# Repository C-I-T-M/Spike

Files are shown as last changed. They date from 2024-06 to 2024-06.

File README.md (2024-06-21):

# Spike
Dentro de este GIT encontrarán todo lo necesario para utilizar y/o armar a spike.

RECOMENDACION: Leer primero el manual técnico y de usuario y después el manual de armado e iniciación. En este último realizar los procesos de forma secuencial (no armar y luego calibrar)

Si consideran que falta información o tienen alguna duda favor de contactarme.
Contacto: citm0220@gmail.com

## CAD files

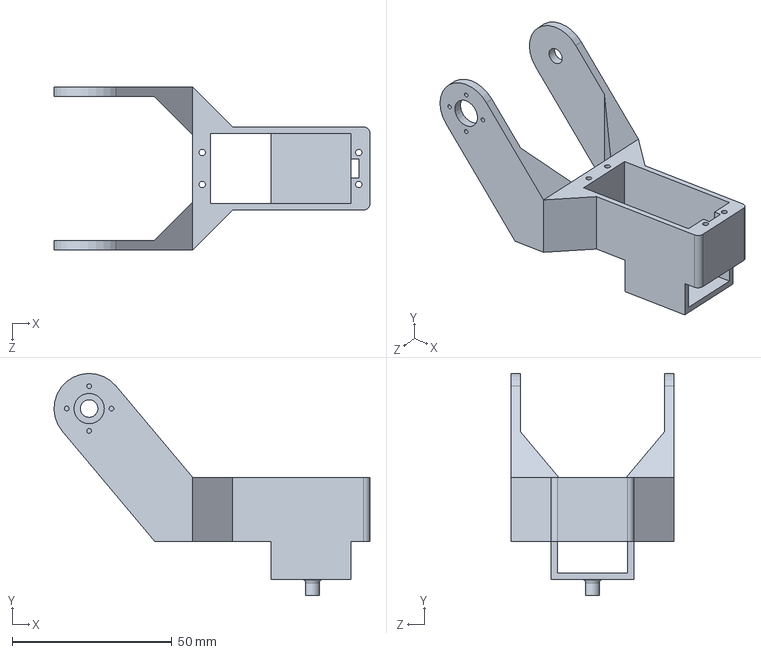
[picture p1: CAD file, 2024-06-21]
Piezas/femur_izquierdo.SLDPRT
98.9 x 69.5 x 51.0 mm

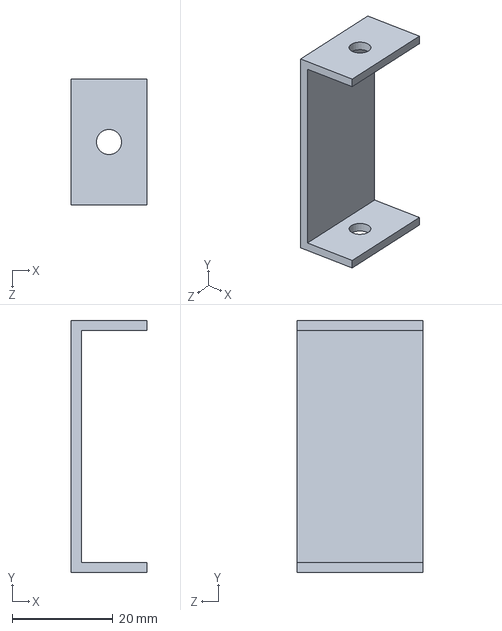
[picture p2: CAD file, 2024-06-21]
Piezas/SoporteLargo.SLDPRT
15.0 x 50.0 x 25.0 mm

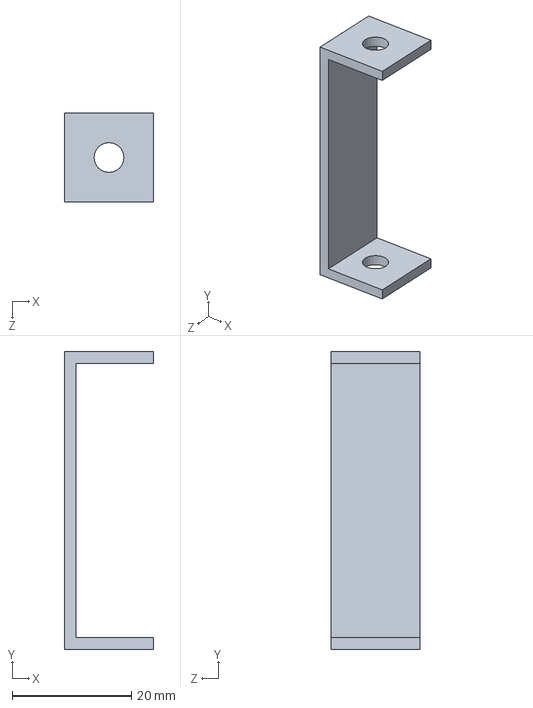
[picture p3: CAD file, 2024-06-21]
Piezas/SoporteCorto.SLDPRT
15.0 x 50.0 x 15.0 mm

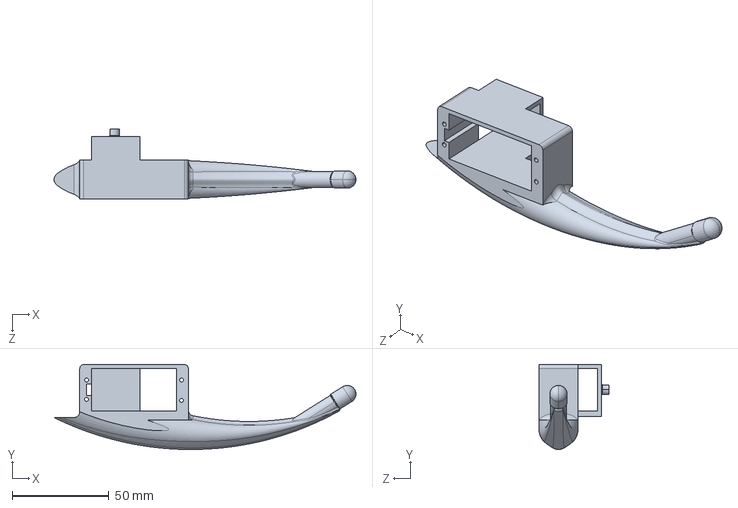
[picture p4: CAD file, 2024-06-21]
Piezas/tarso_izquierdo.SLDPRT
155.8 x 43.8 x 36.3 mm

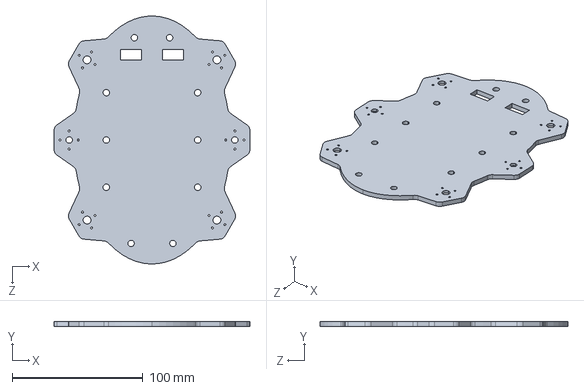
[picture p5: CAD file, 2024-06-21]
Piezas/Base.SLDPRT
150.0 x 3.50 x 190.0 mm

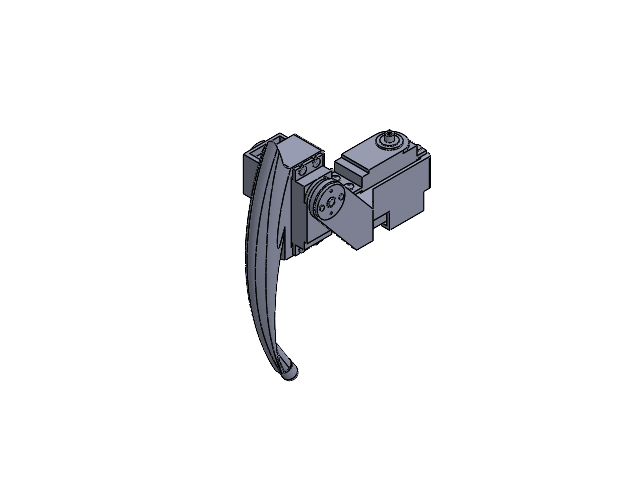
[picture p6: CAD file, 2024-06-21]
Piezas/pata_izquierda.SLDASM
femur_izquierdo
pataai.STEP
conector_cirular
Servomotor x 2
tornillo A
tornillo B x 8
tornillo C x 2

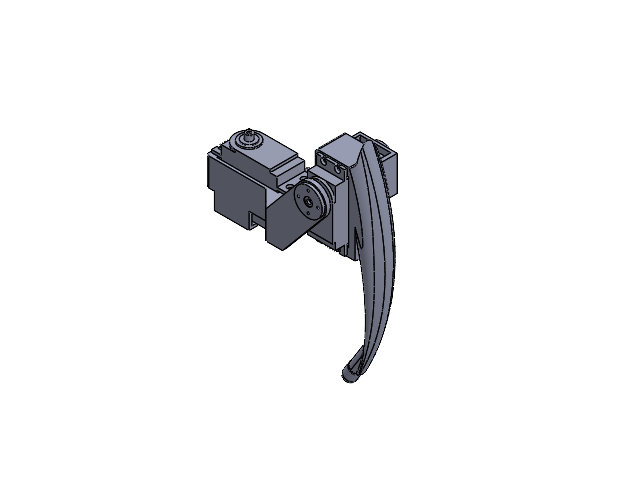
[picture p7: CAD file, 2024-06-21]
Piezas/pata_derecha.SLDASM
conector_cirular
Servomotor x 2
femur_derecho
pataad.step

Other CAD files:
Piezas/femur_derecho.SLDPRT
Piezas/tarso_derecho.SLDPRT

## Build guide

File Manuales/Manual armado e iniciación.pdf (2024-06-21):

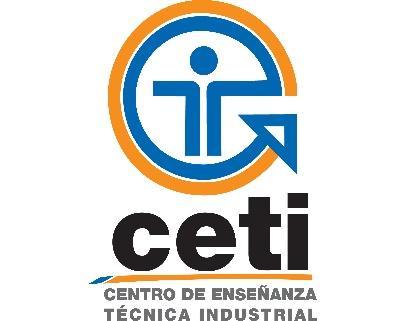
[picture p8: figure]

Spike

CENTRO DE ENSEÑANZA TÉCNICA INDUSTRIAL

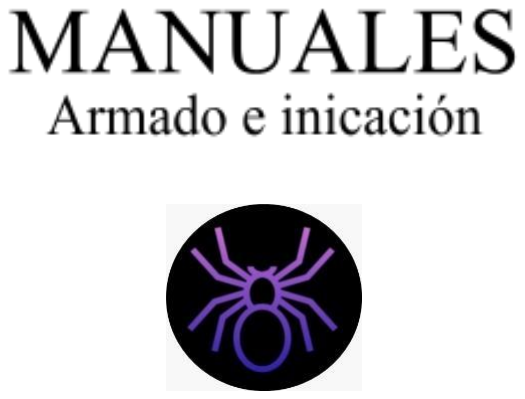
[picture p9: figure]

Alumnos:

Arien Michelle López Jáuregui 20300712

Carlos Isaac Torres Méndez 20300715

Esteban Barboza Ochoa 20300719

Carrera:

Control automático e Instrumentación

Asesor:

Ph.D Alfonso Pérez Gonzales

Asesor externo:
Ing. Carlos Barboza Ochoa
Ph.D. César Méndez García

ÍNDICE

MANUAL ARMADO E INICIACIÓN

INTRODUCCIÓN

En este documento se mostrará y detalla todo lo necesario para el funcionamiento de Spike.

OBJETIVO
Explicar cómo hacer el armado de Spike, cómo hacer la iniciación del robot y las calibraciones que lleguen a ser necesarias para su buen funcionamiento.

LISTA DE PARTES:
Pieza | Cantidad | Imagen

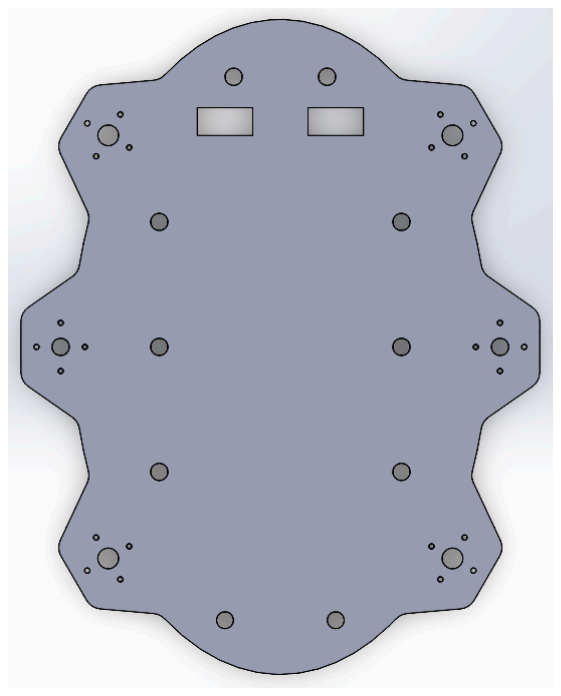
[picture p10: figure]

Base (Imprimir) | 2

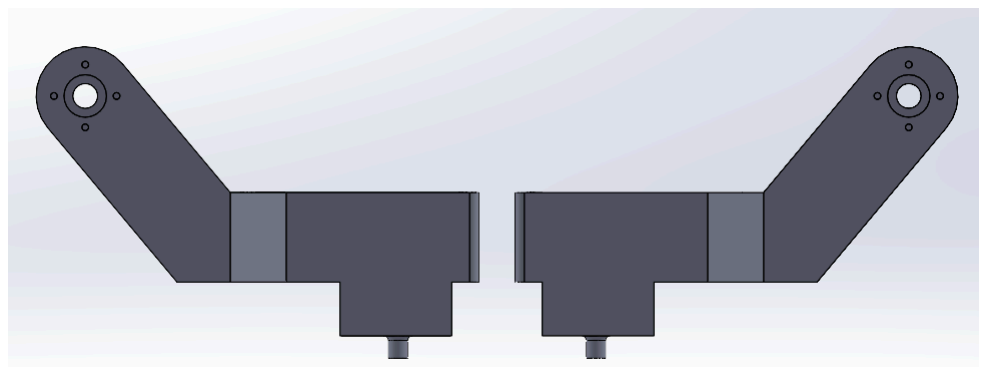
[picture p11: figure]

Fémur (Imprimir) | 3 derecho 3 izquierdo

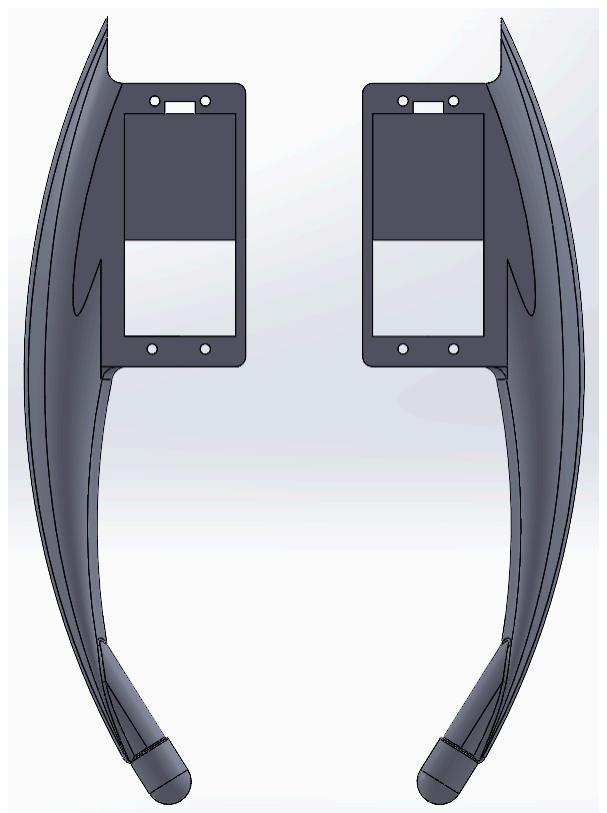
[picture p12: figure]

Tarso (Imprimir) | 3 derecho 3 izquierdo

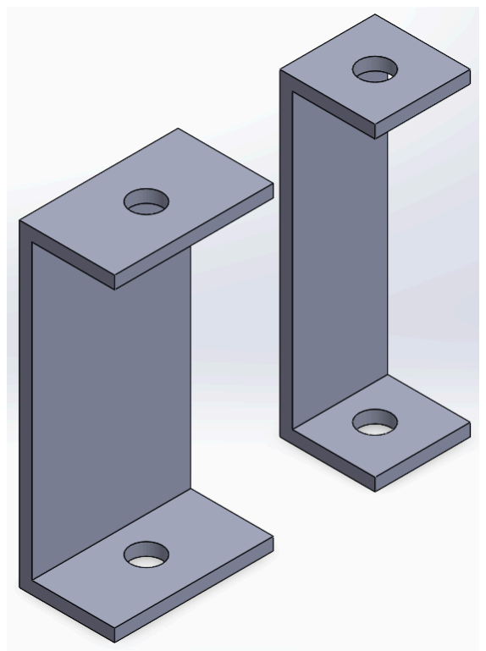
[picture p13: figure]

Soportes | 4 largo 4 corto

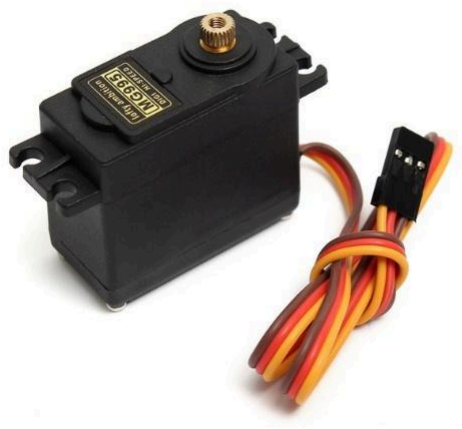
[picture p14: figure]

Servomotor MG995 (compra externa) | 12
Módulo Controlador de servos PCA9685 | 1

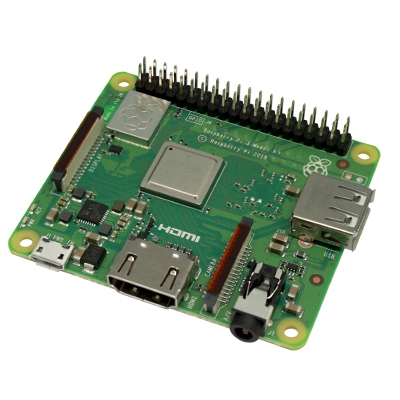
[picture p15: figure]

Raspberry:
Recomendamos
modelos con
bluetooth integrado
(como la PI 3
modelo A+ o la
Zero o Zero 2W) si
se quiere utilizar la
app, en caso de no
querer usar esta
función, se pueden
usar otros modelos.

1

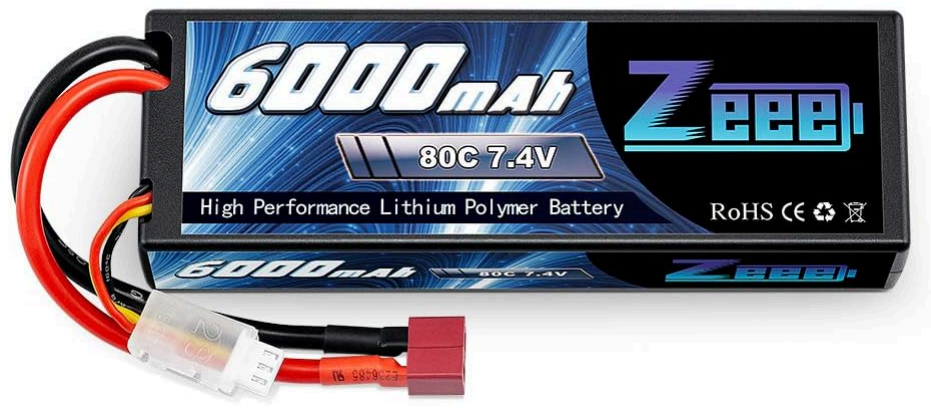
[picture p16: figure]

Batería LiPo | 1

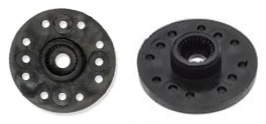
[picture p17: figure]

Conector circular (Incluida en servos) | 12
Tornillo A (Incluido en servos) | 12
Tornillo B (Incluido en servos) | 24

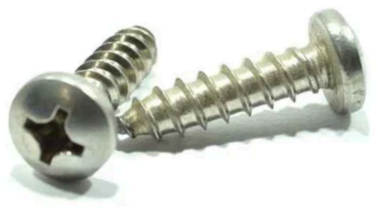
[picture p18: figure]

Tornillo C #2 x 3/8" (compra externa) | 12

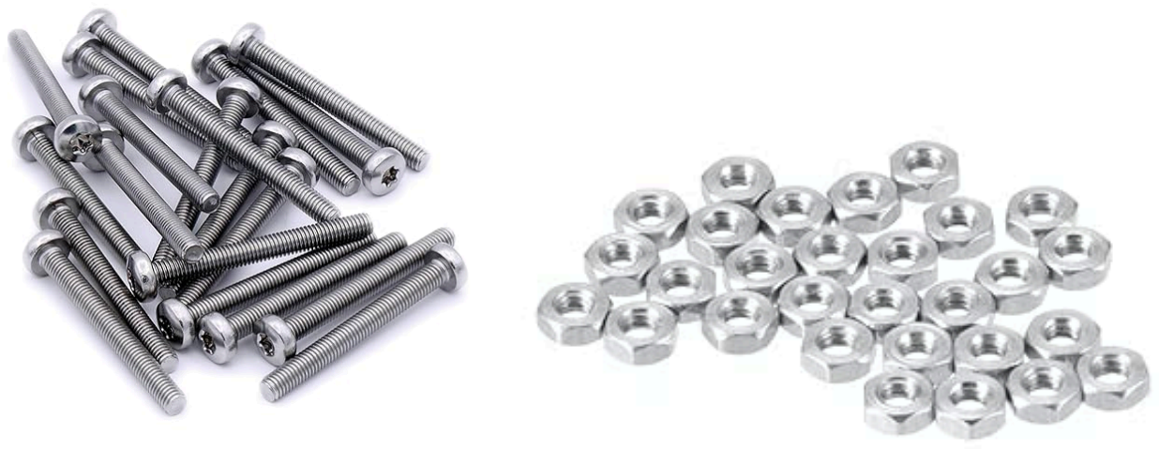
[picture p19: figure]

Tornillo D M1.6 x 10 mm + tuercas (compra externa) | 12
Tornillo E 1/8“ x 1/2 + tuercas (compra externa) | 14

CALIBRACIÓN DE SERVOS:

IMPORTANTE: solo realizar este apartado en caso de usar un modelo de servomotor diferente al MG995.

Para el lograr una calibración de servos seguir los siguientes pasos:

- Investigar la datasheet del servomotor a utilizar y buscar los siguientes datos:
- Frecuencia de funcionamiento.
- pulse width para 0 grados
- pulse width para 180 grados
- Poner el conector circular al servo para que sea más sencillo visualizar los ángulos de los giros.
- Conectar un servo al módulo PCA9685, el cual fue conectado previamente a la raspberry como se muestra en el diagrama de conexión (manual técnico).
- Abrir el código “Motores.py” y realizar lo siguiente:
- En caso de encontrar los valores en la datasheet:
■ Dentro de la variable puls_0 guardar el valor del pulse width para 0 grados. ■ Dentro de la variable puls_180 guardar el valor del pulse width para 180 grados.
■ Dentro de la función pwm.set_pwm_freq() ingresar el valor de la frecuencia de funcionamiento.
■ Iniciar el código y verificar que en efecto el servo gire de 0 a 180 grados, en caso contrario, realizar ajustes a prueba y error de los valores de puls_0 y puls_180.

- En caso de no encontrar los valores en la datasheet, utilizar los puestos en el código como referencia y realizar los ajustes necesarios.

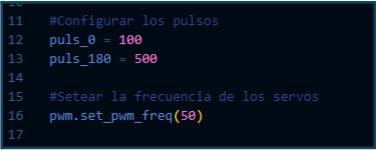
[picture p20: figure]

- El código realizará la siguiente secuencia (se puede modificar la variable de tiempo entre movimientos t si el usuario lo ve necesario):
- Girar 0 grados y esperar
- Girar 90 grados y esperar
- Girar 180 grados y esperar

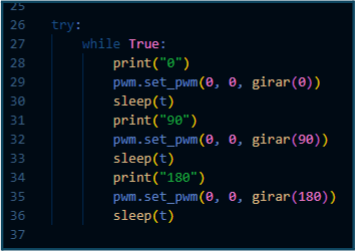
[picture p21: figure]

- La importancia de probar con estos 3 ángulos radica en que podría pasar que los servos giran 0 y 180 grados, pero no tengan el pulse width correcto (sucede cuando se eligen valores menores al correcto de 0 y mayores al correcto de 180), entonces el resto de ángulos no serán correctos. Para ello agregamos el ángulo de 90º.

- Si los tres ángulos son correctos, el servo estará calibrado, en caso contrario realizar las modificaciones necesarias.
- Verificar que funcione correctamente para todos los servomotores que se quieran utilizar.

ARMADO:
Para el apartado de armado del robot seguir los siguientes pasos:
- Conectar los servos al módulo de relevadores previamente conectado a la raspberry. La conexión de servos a módulo puede ser arbitraria.

IMPORTANTE: no tener armada ninguna parte del robot, los servos deben estar sueltos.

- Utilizando el código “Principal.py”, descomentar el bloque “while True”. Dentro de él, descomentar tarsos90() y femurs90(). Deja comentado el resto y corre el código; esto hará que todos los servos tengan un ángulo de 90 grados para poder ser unidos al resto de partes.

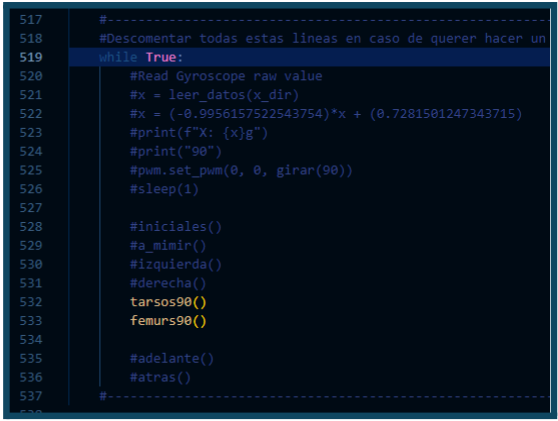
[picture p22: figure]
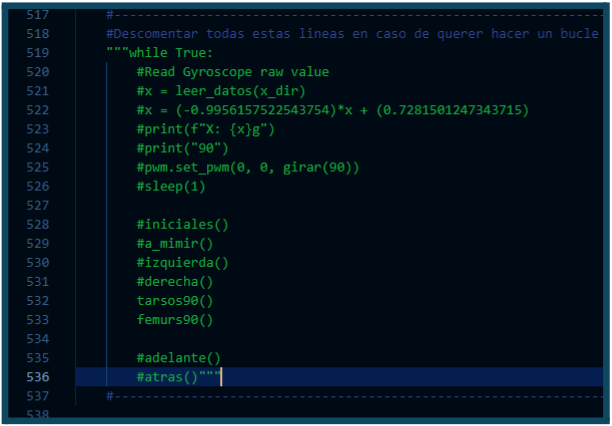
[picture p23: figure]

- Desconectar los servos del módulo y colocarlos en tarso y fémur, asegurándolos con los tornillos B. Unir el conector circular al fémur usando dos tornillos C y agregar la pieza del tarso con su motor usando la pieza circular como conexión, y un tornillo A para asegurar que quede sujeto.

Asegurarse que el motor tenga un ángulo de 90° en relación al fémur, como se muestra en las imágenes de referencia.

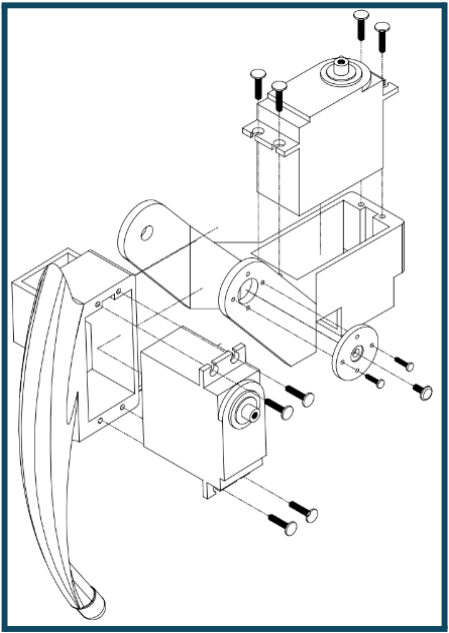
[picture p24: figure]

Repetir este paso con las 6 patas.

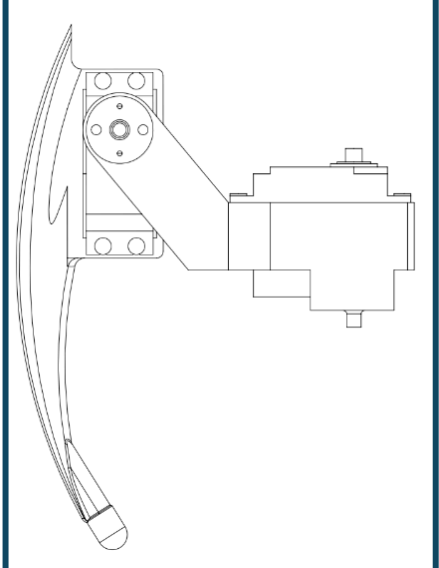
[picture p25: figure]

- Tomar una base, poner los conectores circulares donde se encuentran las hendiduras y asegurarlos bien utilizando los Tornillos D con sus respectivas tuercas.

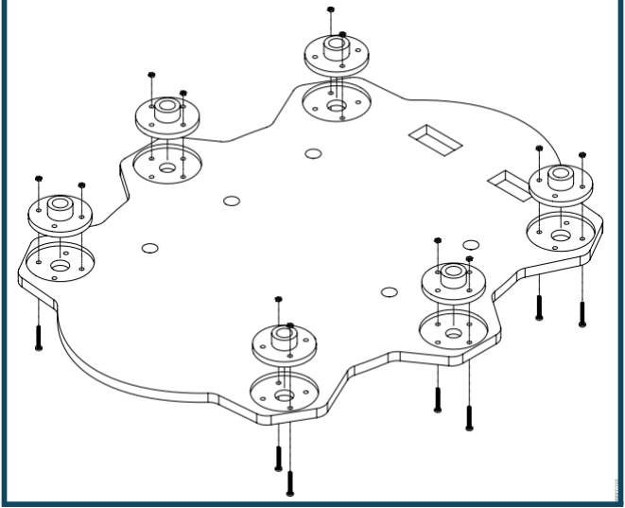
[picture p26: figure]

- Lo siguiente es agregar las piezas de las patas con ayuda de los tornillos A y los conectores circulares.

IMPORTANTE: las patas deben tener un acomodo como se muestra en la imagen.

TIP: conectar los servos de atrás hacia adelante (atrás es donde la base tiene los rectángulos cortados) y cada que se conecte un servo pasar los cables a la parte superior a través de los rectángulos.

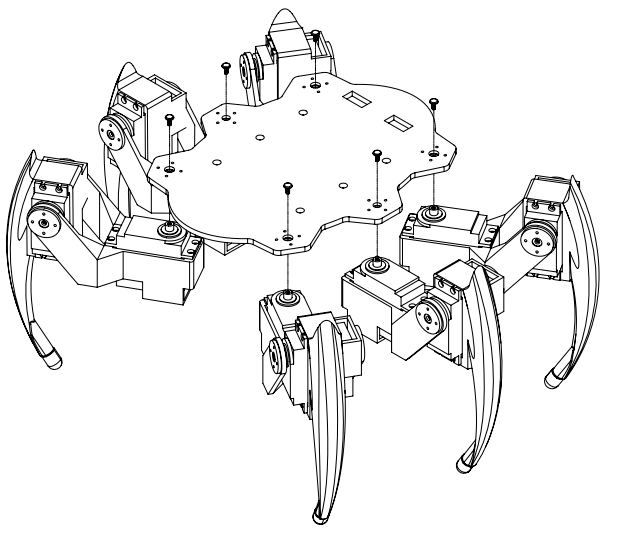
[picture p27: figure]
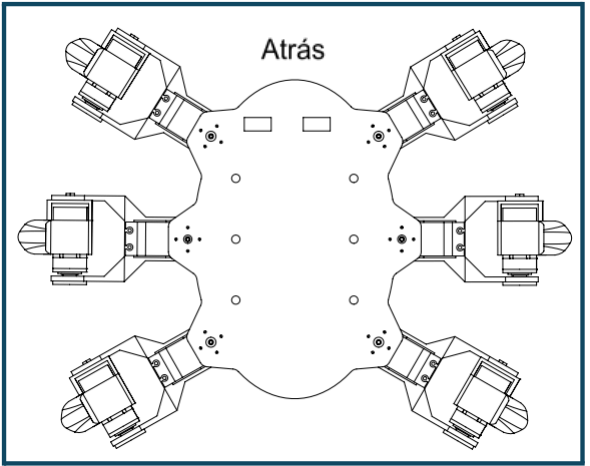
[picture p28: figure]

- Asegurar los soportes a la base con los tornillos E y sus tuercas, deslizar las pilas y colocar los otros dos soportes de la parte de atrás. Después, colocar la otra base y unirla con los tornillos E y sus tuercas a la parte de abajo de los soportes como se muestra en la imagen.

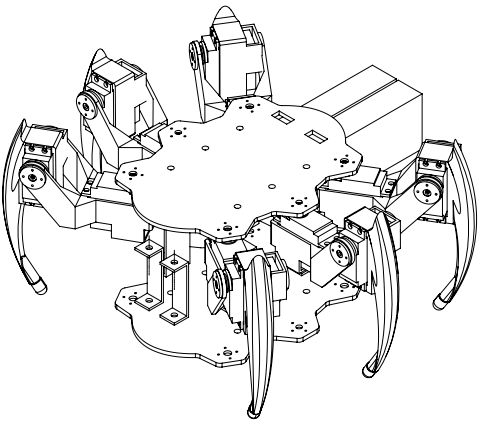
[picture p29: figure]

- Terminando el armado se vería algo así

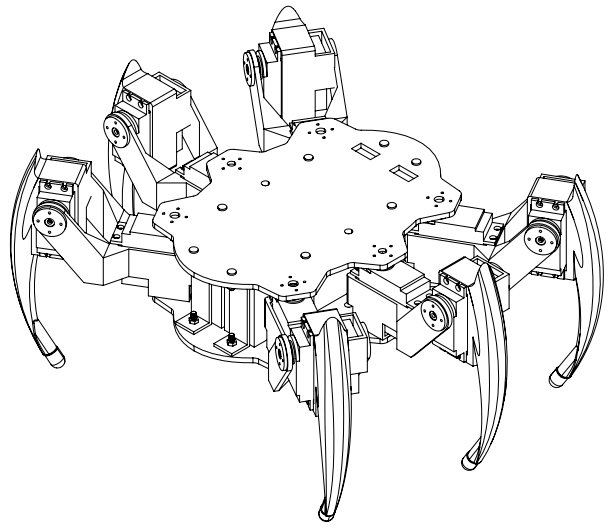
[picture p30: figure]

BLUETOOTH:
Para verificar el bluetooth es necesario que primero descarguen la app BlueDot (solo android (https://bluedot.readthedocs.io/en/latest/bluedotandroidapp.html) o python). (https://bluedot.readthedocs.io/en/latest/bluedotpythonapp.html)

Los pasos para verificar son los siguientes:

- Enlazar el bluetooth del dispositivo en el que tengamos descargada la app con nuestra raspberry. https://descubrearduino.com/wifi-bluetooth-raspberry-pi/
- Abrir el código “BT.py”.
- Iniciar el código en la raspberry, abrir la app BlueDot y verificar que se muestre la siguiente distribución de botones:

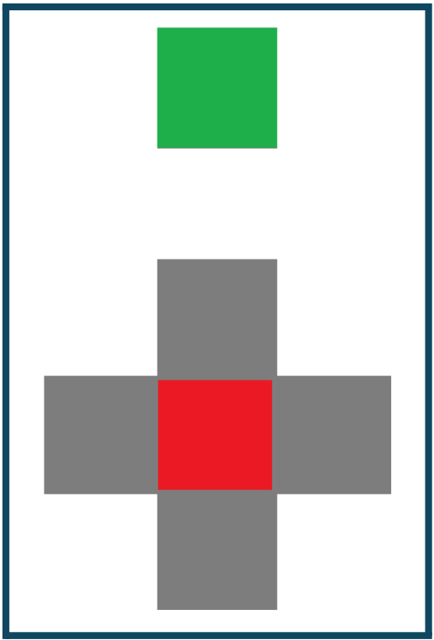
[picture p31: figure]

- El botón verde es el botón de inicio, el botón rojo será nuestro botón de descanso. Usando el rojo como referencia, el botón arriba de él será adelante, a su izquierda botón izquierda, a su derecha botón derecha y hacia abajo botón atrás.
- En la terminal de la raspberry deberá mostrarse la acción presionada en texto, en caso de que se muestran direcciones que no son las presionadas, verificar el código y que no se haya modificado algún punto.
- Si no hay problemas, el bluetooth funciona correctamente.

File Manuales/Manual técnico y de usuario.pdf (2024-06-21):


Control Automático
Propuesta de Proyecto de Titulación

CENTRO DE ENSEÑANZA TÉCNICA INDUSTRIAL

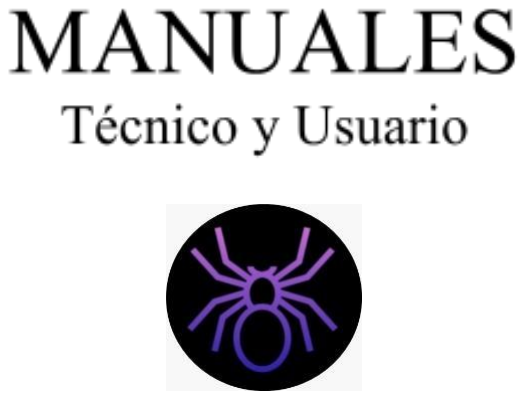
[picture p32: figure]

Alumnos:

Arien Michelle López Jauregui 20300712

Carlos Isaac Torres Méndez 20300715

Esteban Barboza Ochoa 20300719

Carrera:

Control automático e Instrumentación

Asesor:

Ph.D Alfonso Pérez Gonzales

Asesor externo:
Ing. Carlos Barboza Ochoa
Ph.D. César Méndez García

ÍNDICE

MANUAL TECNICO | 5
Introduccion | 5
Objetivo | 5
Conexión del modulo controlador de servos pca9685 | 6
Diagramas de conexión | 7
Material y especificaciones | 7
Ensamblado | 9
MANUAL DE USUARIO | 10
Introduccion | 10
Objetivo | 10
Funcionamiento | 10
Diagrama | 14
Interfaz | 15
Identificación de errores | 16

INTRODUCCION

En este documento se proporciona toda la información necesaria para que el equipo técnico pueda llevar a cabo las tareas de reparación, revisión, calibración y ajuste del sistema. Asimismo, se advierte que esta información debe ser utilizada exclusivamente por personal debidamente capacitado y siguiendo todas las medidas de seguridad pertinentes, especialmente en lo que respecta a la manipulación de la batería de litio.

El contenido del documento incluye los diagramas de conexión correspondientes a la construcción del proyecto.

OBJETIVO

Proveer información detallada, clara y precisa sobre el sistema para garantizar su adecuado uso, mantenimiento y operación por parte del personal técnico especializado.

CONEXIÓN DEL MODULO CONTROLADOR DE SERVOS PCA9685

Pin Modulo Parte | Lado | Zona | Siglas
0 | Fémur | Izquierda | Top | FIT
1 | Tarso | Izquierda | Top | TIT
2 | Fémur | Izquierda | Mid | FIM
3 | Tarso | Izquierda | Mid | TIM
4 | Fémur | Izquierda | Bot | FIB
5 | Tarso | Izquierda | Bot | TIB
6 | Fémur | Derecha | Top | FDT
7 | Tarso | Derecha | Top | TDT
8 | Fémur | Derecha | Mid | FDM

9 | Tarso | Derecha | Mid | TDM
10 | Fémur | Derecha | Bot | FDB
11 | Tarso | Derecha | Bot | TDB

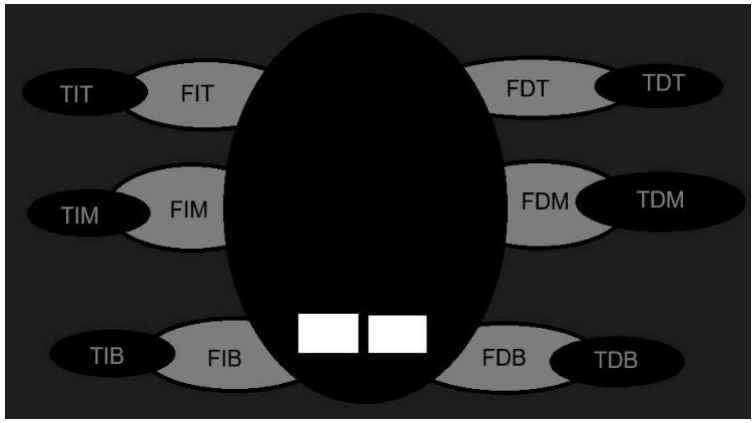
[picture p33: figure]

DIAGRAMAS DE CONEXIÓN

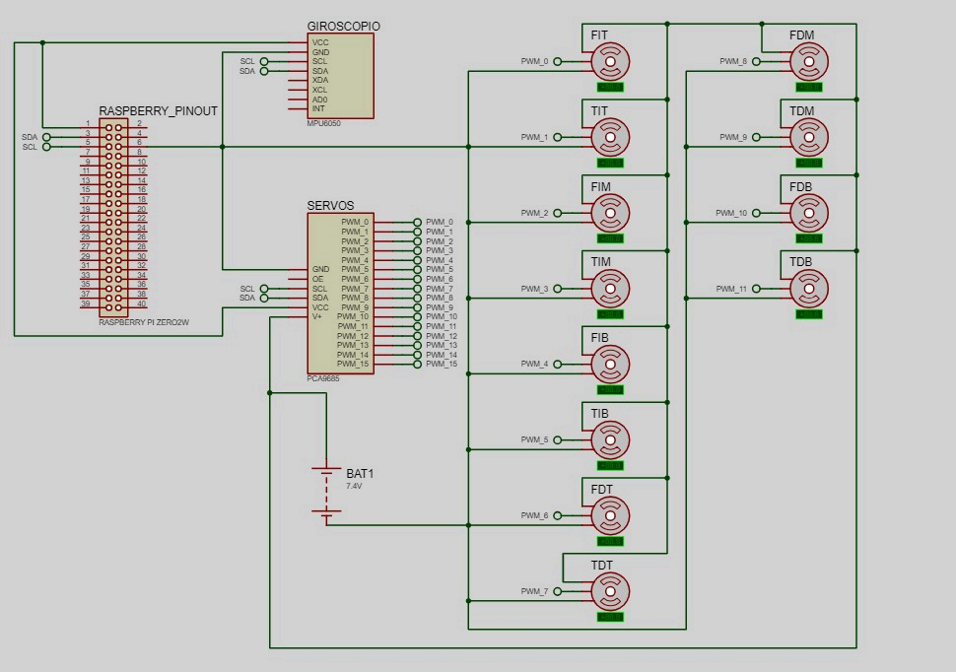
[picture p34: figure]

MATERIAL Y ESPECIFICACIONES

Material | Especificaciones
Raspberry Pi Zero 2W

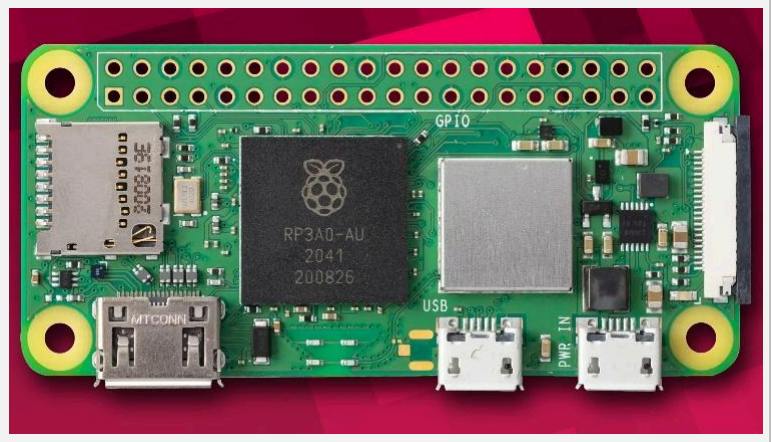
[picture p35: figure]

ESTE MODELO PUEDE PRESENTAR PROBLEMAS DE HARDWARE, UN MODELO MÁS CARO PERO MÁS SEGURO ES LA RASPBERRY PI 3 MODELO A+

-Procesador quad-core a 1GHz de 64-bit, basado en el ARM Cortex-A53 -GPU VideoCore IV
-DRAM de 512MB LPDDR2
-Red inalámbrica WLAN 802.11b/g/n a 2.4GHz
Bluetooth 4.2 / Bluetooth Low Energy (BLE)
- Entrada para MicroSD
-Puertos Mini HDMI y USB 2.0 OTG -Entrada Micro USB para alimentar la tarjeta
-Header GPIO de 40 pines compatible con HATs

https://www.agelectronica.com/detalle.php?p=RASPBERRYPI-3-MODAP&src=raspberrypi (https://www.agelectronica.com/detalle.php?p=RASPBERRYPI-3-MODAP&src=raspberrypi) | -Video compuesto y pines para resetear la tarjeta, a través de pistas de cobre -Conector para cámara CSI -Voltaje de Alimentacion: 5V DC -Corriente: 2.5 A -Temperatura de Operacion: -20°C-70°C
Modulo Controlador de Servos PCA9685 | -Voltaje de alimentación: 5V DC -Máxima corriente por pin: 25 mA -Interfaz: I2C -Resolución: 12 bits -Número de canales: 16 -Frecuencia de operación: 40 Hz a 1000 Hz -Protección: Inversión de Voltaje -Dimensiones: 62 mm x 26 mm -Peso: 12g

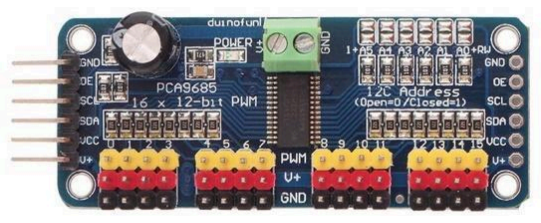
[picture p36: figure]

Giroscopio MPU-6050
-VDD= 2.375V-3.46V
-VLOGIC(MOU-6050)=1.8V±5%
-T =25°C A

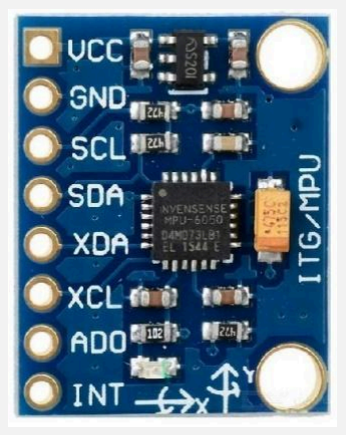
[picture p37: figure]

Servomotor MG995 | -Voltaje de operación: 5.7 ~ 7.2 V -Tipo de Interfaz: Analógica -Giro: 180º -Velocidad de Operación (5.7 V sin carga): 0.2 seg. / 60º -Velocidad de Operación (7.2 V sin carga): 0.16 seg. / 60º -Rango de Temperatura: - 30 ~ 60 C -Corriente de funcionamiento: 100 mA -Par de funcionamiento: 15 kg / cm

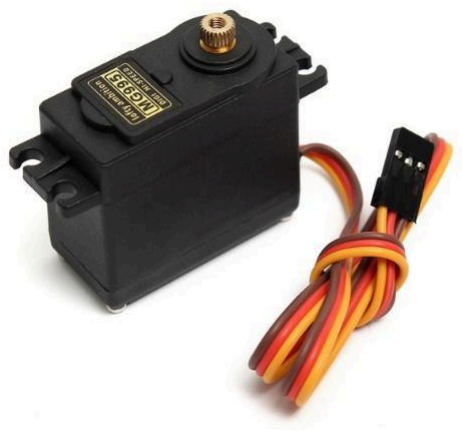
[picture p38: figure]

Bateria Lipo Zeee 2S | -Voltaje: 7.4V -Configuración: 2S1P -Capacidad: 2200 mAh -Descarga: 50C

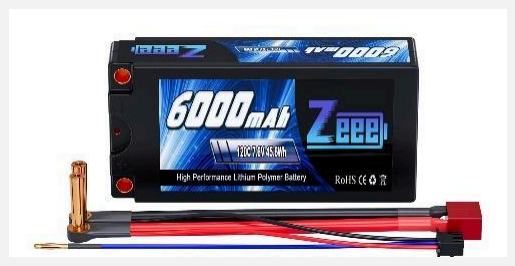
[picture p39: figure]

ENSAMBLADO

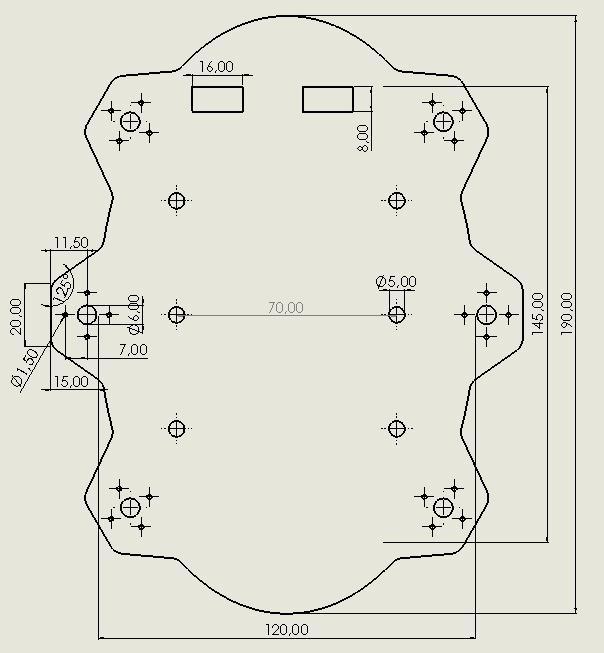
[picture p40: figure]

Base

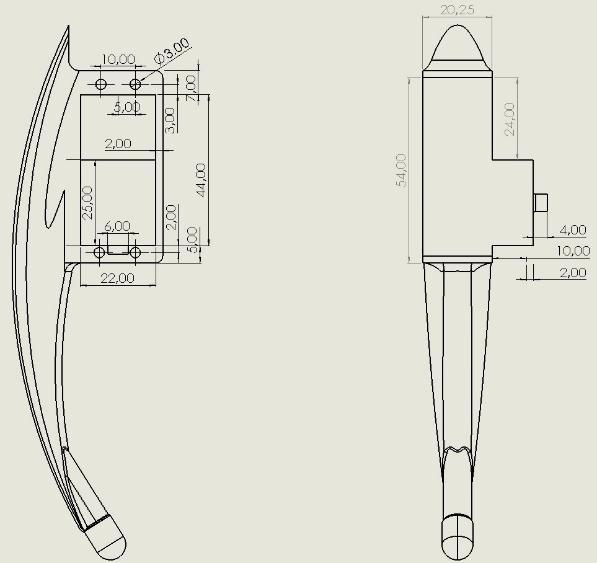
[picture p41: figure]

Tarso

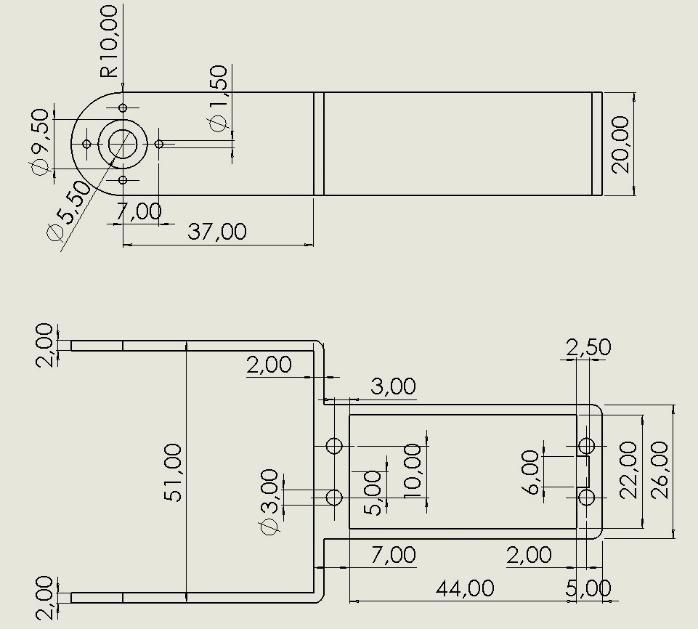
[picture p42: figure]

Fémur

INTRODUCCION

En el presente documento se proporciona toda la información necesaria para una comprensión integral del sistema, facilitando su correcta implementación y uso. Se ofrecerá una explicación clara y precisa de su funcionamiento, detallando cada uno de los pasos que realiza para alcanzar sus objetivos. De esta manera, se pretende que la descripción sea suficientemente clara para que el usuario pueda utilizar el sistema con un entendimiento profundo, más allá de la mera intuición.

El documento incluye una descripción detallada del funcionamiento general del sistema. Se explicará la interfaz, se proporcionará una lista de posibles errores que podrían ocurrir durante la implementación, junto con sus respectivas soluciones, para asegurar una experiencia de usuario óptima y sin contratiempos.

OBJETIVO
Brindar una explicación detallada y comprensiva que permita un uso correcto del sistema, asegurando que el usuario adquiera un conocimiento adecuado de su funcionamiento

FUNCIONAMIENTO
Una vez conectada la batería, la araña dejara de estar en su posición inicial (con sus patas cerradas) y pasara a estar en su posición de caminar (con sus patas abiertas).

Seleccionar en el menú el movimiento deseado de la araña. Al terminar de usarlo seleccionar en el menú la posición inicial antes de apagarlo desconectando la batería.

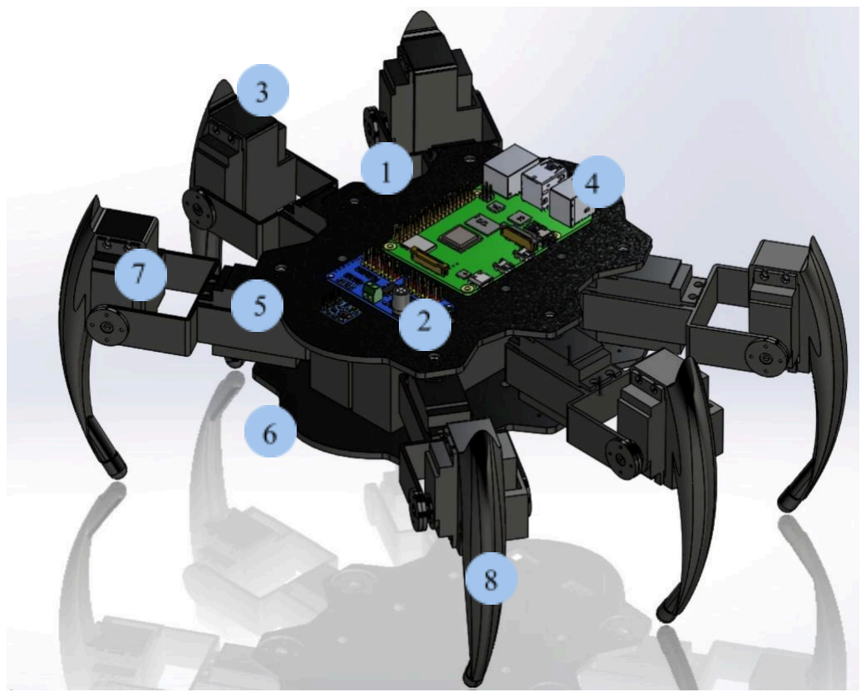
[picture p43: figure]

PARTES DEL ROBOT

1. Raspberry Pi

La Raspberry Pi es un microcontrolador que sirve como el cerebro del sistema. Este pequeño pero potente dispositivo se encarga de mandar las instrucciones necesarias para que la araña robótica realice las acciones señaladas. Gracias a su capacidad de procesamiento y su compatibilidad con múltiples lenguajes de programación, la Raspberry Pi puede controlar los movimientos de la araña, coordinar las señales de los sensores y manejar la comunicación con otros dispositivos. Además, su conectividad a Internet permite actualizaciones remotas y la posibilidad de controlar la araña a distancia.

2. Módulo de Servomotores

El módulo de servomotores es una placa donde se conectan todos los servomotores de la araña robótica. Este módulo distribuye la energía y las señales de control desde la Raspberry Pi hacia los servomotores individuales, permitiendo un control preciso de cada articulación de la araña. Este módulo no solo facilita la organización y conexión de los motores, sino que también incluye características de protección contra sobrecorriente y sobrevoltaje para asegurar un funcionamiento seguro y confiable.

3. Servomotores

Los servomotores son componentes cruciales en la araña robótica, ya que se encargan de transmitir movimiento en forma angular a las distintas partes de las patas, como el fémur y el tarso. Estos motores permiten un control preciso del ángulo y la velocidad de rotación, lo que es esencial para la movilidad y estabilidad del robot. Los servomotores reciben señales del módulo y las traducen en movimientos específicos, permitiendo que la araña se desplace de manera fluida y coordinada.

4. Cuerpo

El cuerpo de la araña es la estructura central donde se colocan todos los componentes eléctricos, incluyendo la Raspberry Pi, el módulo de servomotores, y otros sensores y circuitos necesarios. Este cuerpo está diseñado para ser robusto y ligero, proporcionando protección a los componentes internos y una base estable para las patas de la araña.

5. Brújula

La brújula es un sensor crucial que indica la orientación del cuerpo de la araña robótica en relación con los puntos cardinales. Este dispositivo permite que la araña mantenga un sentido de dirección preciso, facilitando la navegación y la ejecución de movimientos coordinados.

6. Pila

La pila, o batería, es un componente esencial del cuerpo de la araña, ya que proporciona la energía necesaria para el funcionamiento de todos los sistemas electrónicos. El cuerpo de la araña cuenta con un compartimento especialmente diseñado para alojar la batería, asegurando una distribución equilibrada del peso y fácil acceso para la carga o reemplazo.

7. Fémur

El fémur es la parte de la pata de la araña que actúa como una unión entre el cuerpo y el tarso. Esta sección es crucial para la movilidad de la araña, ya que permite la articulación y el movimiento de las patas en diferentes ángulos

8. Tarso

El tarso es la parte final de la pata de la araña, y es responsable de proporcionar el contacto con el suelo.

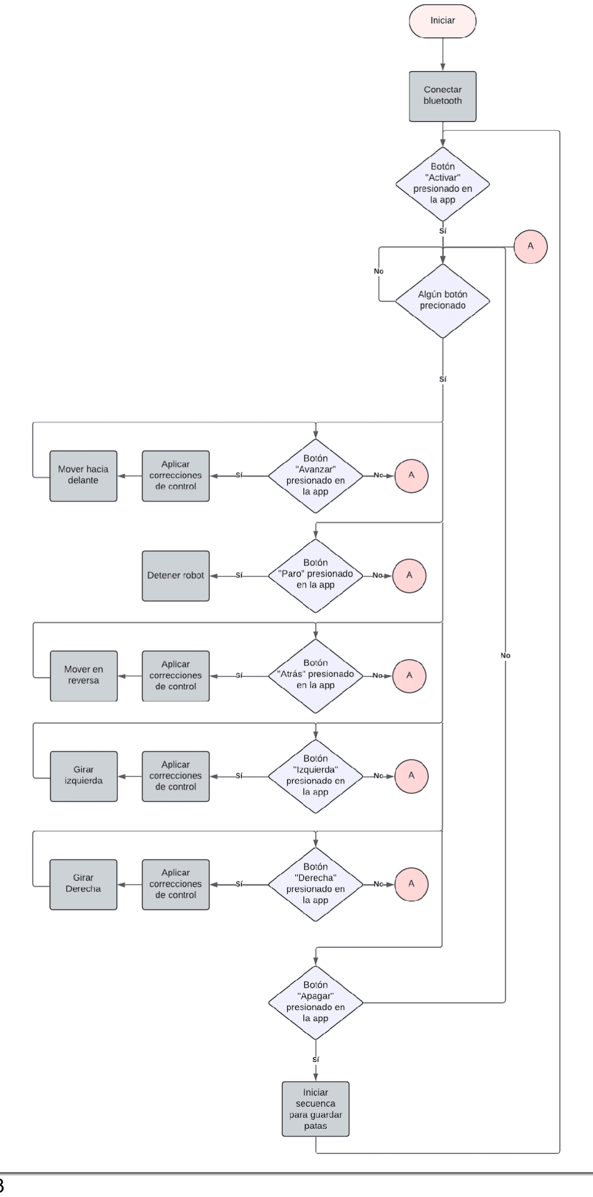
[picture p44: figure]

DIAGRAMA

INTERFAZ

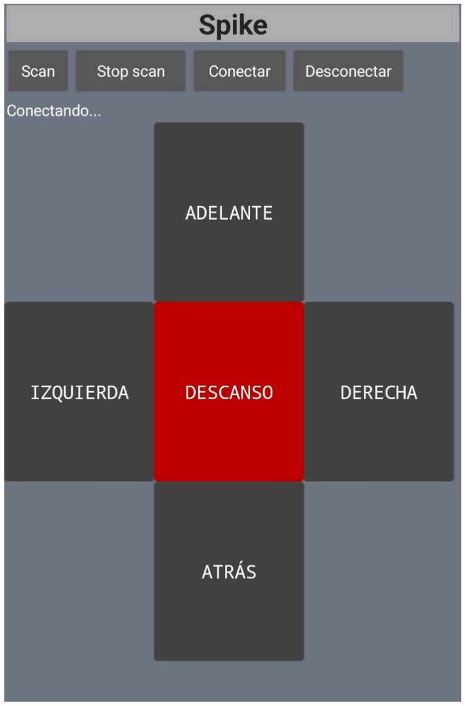
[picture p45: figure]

En la pantalla se muestra un menú de opciones de los cuales podrás elegir la opción deseada para que Spike realice la acción(movimiento).

IDENTIFICACIÓN DE ERRORES

- Spike no quiere encender

En primer lugar, se deberá revisar detalladamente la condición de la batería. Esto implica verificar su nivel de carga, inspeccionar posibles signos de desgaste, corrosión o daño físico en la batería y asegurarse de que esté bien conectada. Es importante comprobar que no haya conexiones sueltas o cables dañados que puedan estar impidiendo el flujo de corriente adecuado. Si tras esta revisión se determina que la batería no es el problema, lo siguiente será la revisión de las conexiones del sistema, tomando en cuenta el manual técnico. Esto incluye verificar los fusibles, interruptores y todos los componentes eléctricos que puedan estar interfiriendo con el encendido de Spike. Además, se puede utilizar un multímetro para medir voltajes en diferentes puntos y asegurarse de que todos los componentes estén recibiendo la energía necesaria.

- Servos no avanzan

Revisar conexiones y alimentaciones. Asegurarse de que todos los cables estén firmemente conectados y que no haya interrupciones en el suministro de energía. En caso de que esto no sea el problema, revisar el código fuente y verificar que la asignación de pines sea correcta. Es fundamental asegurarse de que los pines configurados en el software correspondan a los pines físicos utilizados en el hardware. Si después de estas verificaciones los servos aún no avanzan, checar el protocolo I2C. Esto incluye revisar que los dispositivos en el bus I2C tengan direcciones únicas y que no haya conflictos en el bus. Además, se debe confirmar que el código esté enviando y recibiendo datos correctamente a través del I2C y que no haya errores de comunicación.

- Sensor no detecta

Checar conexiones y el protocolo I2C. Asegurarse de que todos los cables estén correctamente conectados y que no haya fallas en el bus de comunicación. Si no funciona, verificar el modelo de la brújula y revisar las direcciones de envío de datos de la brújula (consultar el datasheet de la brújula). Es crucial asegurarse de que el código esté configurado para comunicarse correctamente con el sensor específico y que las direcciones utilizadas en el software coincidan con las del hardware. Además, puede ser útil realizar pruebas con un sensor de reemplazo para descartar posibles defectos en el sensor original. También, asegurarse de que el entorno en el que se encuentra el sensor no esté afectando su funcionamiento, como interferencias electromagnéticas o presencia de materiales metálicos que puedan distorsionar las lecturas.

- Desajuste de ángulos de los servos

Poner 90° en tarsos y fémur y verificar que estén bien ensamblados. Asegurarse de que los componentes mecánicos estén correctamente alineados y que no haya holguras o partes sueltas que puedan afectar el ángulo de los servos. En caso de que esto no resuelva el problema, verificar el código. Esto implica asegurarse de que los valores de posición enviados a los servos sean correctos y que no haya errores en los cálculos de los ángulos. Además, se puede realizar una calibración manual de los servos para asegurarse de que respondan adecuadamente a las señales de control. También, es útil revisar las especificaciones técnicas de los servos para confirmar que estén operando dentro de sus límites de funcionamiento y que no estén siendo forzados más allá de sus capacidades.

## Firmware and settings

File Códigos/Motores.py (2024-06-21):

#Librerias externas:
import Adafruit_PCA9685 as modulo;	"""Información: https://github.com/adafruit/Adafruit_Python_PCA9685"""
import smbus;						"""Información: https://www.engineersgarage.com/articles-raspberry-pi-i2c-bus-pins-smbus-smbus2-python/"""

#Librerias internas:
from time import sleep;        		"""Información: https://docs.python.org/3/library/time.html"""
import math;						"""Información: https://docs.python.org/3/library/math.html"""

add = 0x68   # Address del sensor (usar "sudo i2cdetect -y 1" en la terminar para detectar la dirección de los componentes i2c)

#Iniciar PCA9685 con su default address (0x40)	
pwm = modulo.PCA9685(0x40)

#Configurar los pulsos
puls_0 = 100
puls_180 = 500

#Setear la frecuencia de los servos
pwm.set_pwm_freq(50)

#tiempo entre movimientos (segundos):
t = 1


def girar(angulo):
	return  int(puls_0 + (angulo/180)*(puls_180-puls_0))

	
try:
	while True:	
		print("0")
		pwm.set_pwm(0, 0, girar(0))
		sleep(t)
		print("90")
		pwm.set_pwm(0, 0, girar(90))
		sleep(t)
		print("180")
		pwm.set_pwm(0, 0, girar(180))
		sleep(t)
				
		
		
except KeyboardInterrupt:
	for i in range(15):
		pwm.set_pwm(i, 0, 0)

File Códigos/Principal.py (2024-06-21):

#Librerias externas:
import Adafruit_PCA9685 as modulo;	"""Información: https://github.com/adafruit/Adafruit_Python_PCA9685"""
from bluedot import BlueDot;		"""Información: https://bluedot.readthedocs.io/en/latest/gettingstarted.html"""
import smbus;						"""Información: https://www.engineersgarage.com/articles-raspberry-pi-i2c-bus-pins-smbus-smbus2-python/"""

#Librerias internas:
from time import sleep;        		"""Información: https://docs.python.org/3/library/time.html"""
import math;						"""Información: https://docs.python.org/3/library/math.html"""
from signal import pause;			"""Información: https://docs.python.org/3/library/signal.html"""

#Registros y direcciones para el sensor MPU (buscar en datasheet en caso de usar otro modelo)
power = 0x6B
sample_rate = 0x19
conf = 0x1A
gyro_conf = 0x1B
interrup = 0x38
x_dir  = 0x3B
y_dir  = 0x3D
z_dir  = 0x3F

add = 0x68   # Address del sensor (usar "sudo i2cdetect -y 1" en la terminar para detectar la dirección de los componentes i2c)

#Iniciar PCA9685 con su default address (0x40)	
pwm = modulo.PCA9685(0x40)

#Configurar los pulsos de los servos para 0 y 180 grados (calibrado usando los pasos del manual Armado e Iniciación, sección "Calibración de servos")
puls_0 = 100
puls_180 = 500

#Setear la frecuencia de los servos (dependen del servo, checar datasheets)
pwm.set_pwm_freq(50)

"""Vectores de combinaciones posibles:"""
TODO = range(0, 12) 					#El rango va dependiendo de las conexiones de los servos en el modulo PCA9685
	
#Separar por lado  						(revisar documento de conexiones para saber cual es cual)
Izquierda = range(0, 6)
Derecha = range(6, 12)

#Separar por partes
femurs = range(10, -1, -2)
tarsos = range(1, 12, 2)

#Separado partes y lado
femur_I = [0, 2, 4]
tarso_I = [1, 3, 5]
femur_D = [6, 8, 10]
tarso_D = [7, 9, 11]

"""Partes independientes: """ 
FIT, TIT, FIM, TIM, FIB, TIB, FDT, TDT, FDM, TDM, FDB, TDB = TODO
	
#Tiempo entre movimientos (Segundos)
t = 0.08

"""Angulos ideales"""
up_d = 124
up_i = 51
down_d = 110
down_i = 70
delante_i = 105
delante_d = 75
detras_i = 75
detras_d = 105

"""------------------------------------------------------------------------------------------------------------------"""
"""Funciones: """
def girar(angulo):		#Mapeo de angulos 
	return  int(puls_0 + (angulo/180)*(puls_180-puls_0))

def avanzar():			#Avanzar levantando 3 a la vez (ideal si spike puede levantar las patas)
	print("Vuelta izquierda: ")
	print("Levantar tarsos derecha, bajar izquierda")
	#Tarsos izquierda
	pwm.set_pwm(TIT, 0, girar(down_i))
	sleep(t)
	pwm.set_pwm(TDM, 0, girar(down_d))
	sleep(t)
	pwm.set_pwm(TIB, 0, girar(down_i))
	sleep(t)
	#Tarsos derecha
	pwm.set_pwm(TDT, 0, girar(up_d))
	sleep(t)
	pwm.set_pwm(TIM, 0, girar(up_i))
	sleep(t)
	pwm.set_pwm(TDB, 0, girar(up_d))
	sleep(t)
	
	print("Delante femurs derecha, atras izquierda")
	#Femrus derecha
	pwm.set_pwm(FDT, 0, girar(delante_d))
	sleep(t)
	pwm.set_pwm(FIM, 0, girar(delante_i))
	sleep(t)
	pwm.set_pwm(FDB, 0, girar(delante_d))
	sleep(t)
	#Femurs izquierda
	pwm.set_pwm(FIT, 0, girar(90))
	sleep(t)
	pwm.set_pwm(FDM, 0, girar(90))
	sleep(t)
	pwm.set_pwm(FIB, 0, girar(90))
	sleep(t)
	
	print("Bajar tarsos derecha, levantar izxquierda")
	#Tarsoso derecha
	pwm.set_pwm(TDT, 0, girar(down_d))
	sleep(t)
	pwm.set_pwm(TIM, 0, girar(down_i))
	sleep(t)
	pwm.set_pwm(TDB, 0, girar(down_d))
	sleep(t)
	#Tarsos izquierda
	pwm.set_pwm(TIT, 0, girar(up_i))
	sleep(t)
	pwm.set_pwm(TDM, 0, girar(up_d))
	sleep(t)
	pwm.set_pwm(TIB, 0, girar(up_i))
	sleep(t)
	
	print("Avanzan los de derecha, los de izqueirda pa atras")
	#Femurs derecha
	pwm.set_pwm(FDT, 0, girar(90))
	sleep(t)
	pwm.set_pwm(FIM, 0, girar(90))
	sleep(t)
	pwm.set_pwm(FDB, 0, girar(90))
	sleep(t)
	#Femurs izquierda
	pwm.set_pwm(FIT, 0, girar(delante_i))
	sleep(t)
	pwm.set_pwm(FDM, 0, girar(delante_d))
	sleep(t)
	pwm.set_pwm(FIB, 0, girar(delante_i))
	sleep(t)
	
	print("Secuencia terminada")
	print("Reiniciando...")

def retroceder():		#Retroceder levantando 3 a la vez (ideal si spike puede levantar las patas)
	print("Vuelta izquierda: ")
	print("Levantar tarsos derecha, bajar izquierda")
	#Tarsos izquierda
	pwm.set_pwm(TIT, 0, girar(down_i))
	sleep(t)
	pwm.set_pwm(TDM, 0, girar(down_d))
	sleep(t)
	pwm.set_pwm(TIB, 0, girar(down_i))
	sleep(t)
	#Tarsos derecha
	pwm.set_pwm(TDT, 0, girar(up_d))
	sleep(t)
	pwm.set_pwm(TIM, 0, girar(up_i))
	sleep(t)
	pwm.set_pwm(TDB, 0, girar(up_d))
	sleep(t)
	
	print("Delante femurs derecha, atras izquierda")
	#Femrus derecha
	pwm.set_pwm(FDT, 0, girar(detras_d))
	sleep(t)
	pwm.set_pwm(FIM, 0, girar(detras_i))
	sleep(t)
	pwm.set_pwm(FDB, 0, girar(detras_d))
	sleep(t)
	#Femurs izquierda
	pwm.set_pwm(FIT, 0, girar(90))
	sleep(t)
	pwm.set_pwm(FDM, 0, girar(90))
	sleep(t)
	pwm.set_pwm(FIB, 0, girar(90))
	sleep(t)
	
	print("Bajar tarsos derecha, levantar izxquierda")
	#Tarsoso derecha
	pwm.set_pwm(TDT, 0, girar(down_d))
	sleep(t)
	pwm.set_pwm(TIM, 0, girar(down_i))
	sleep(t)
	pwm.set_pwm(TDB, 0, girar(down_d))
	sleep(t)
	#Tarsos izquierda
	pwm.set_pwm(TIT, 0, girar(up_i))
	sleep(t)
	pwm.set_pwm(TDM, 0, girar(up_d))
	sleep(t)
	pwm.set_pwm(TIB, 0, girar(up_i))
	sleep(t)
	
	print("Avanzan los de derecha, los de izqueirda pa atras")
	#Femurs derecha
	pwm.set_pwm(FDT, 0, girar(90))
	sleep(t)
	pwm.set_pwm(FIM, 0, girar(90))
	sleep(t)
	pwm.set_pwm(FDB, 0, girar(90))
	sleep(t)
	#Femurs izquierda
	pwm.set_pwm(FIT, 0, girar(detras_i))
	sleep(t)
	pwm.set_pwm(FDM, 0, girar(detras_d))
	sleep(t)
	pwm.set_pwm(FIB, 0, girar(detras_i))
	sleep(t)
	
	print("Secuencia terminada")
	print("Reiniciando...")

def adelante():			#Avanzar moviendo una pata a la vez hacia delante y luego regresando todas para que se arrastre (ideal si spike no puede levantas las patas)
	for i in femur_I:
		pwm.set_pwm(i+1, 0, girar(up_i))
		sleep(t)
		pwm.set_pwm(i, 0, girar(delante_i))
		sleep(t)
		pwm.set_pwm(i+1, 0, girar(down_i))
		sleep(t)
		pwm.set_pwm(i+7, 0, girar(up_d))
		sleep(t)
		pwm.set_pwm(i+6, 0, girar(delante_d))
		sleep(t)
		pwm.set_pwm(i+7, 0, girar(down_d))
		sleep(t)
		
	for i in femur_D:
		pwm.set_pwm(i, 0, girar(detras_d))
		sleep(t)
	for i in femur_I:
		pwm.set_pwm(i, 0, girar(detras_i))
		sleep(t)

def atras():			#Retroceder moviendo una pata a la vez hacia delante y luego regresando todas para que se arrastre (ideal si spike no puede levantas las patas)
	for i in femur_I:
		pwm.set_pwm(i+1, 0, girar(up_i))
		sleep(t)
		pwm.set_pwm(i, 0, girar(detras_i))
		sleep(t)
		pwm.set_pwm(i+1, 0, girar(down_i))
		sleep(t)
		pwm.set_pwm(i+7, 0, girar(up_d))
		sleep(t)
		pwm.set_pwm(i+6, 0, girar(detras_d))
		sleep(t)
		pwm.set_pwm(i+7, 0, girar(down_d))
		sleep(t)
		
	for i in femur_D:
		pwm.set_pwm(i, 0, girar(delante_d))
		sleep(t)
	for i in femur_I:
		pwm.set_pwm(i, 0, girar(delante_i))
		sleep(t)

def tarsos90():			#Poner los tarsos en 90 grados
	for i in tarsos:
		print("90")
		pwm.set_pwm(i, 0, girar(90))
		sleep(t)
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
